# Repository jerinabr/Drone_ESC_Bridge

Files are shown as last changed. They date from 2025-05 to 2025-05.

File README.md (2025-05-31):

# Drone_ESC_Bridge
## Description
This board is intended to act as a bridge between the Nvidia Jetson and the 4-in-1 ESC on the ADP drone[^1]

It recieves motor speeds and other commands from the Jetson over the SPI interface and outputs motor speeds to the ESC over PWM

It also monitors the LiPo voltage and can report it back to the Jetson over the SPI interface

The board receives 5V power from an off-board buck converter which is used to power both the microcontroller (Seeed XIAO SAMD21) and the Jetson

[^1]: Firmware for the Jetson and Seeed XIAO can be found [here](https://github.com/LarsGart/Autonomous-Drone-Platform)

## BOM
| Reference | Value | Footprint | Qty | DigiKey Part Number |
| --- | --- | --- | --- | --- |
| C1,C2,C4,C6,C7,C8 | 0.1u | Capacitor_SMD:C_0603_1608Metric_Pad1.08x0.95mm_HandSolder | 6 | 311-1088-1-ND |
| C3 | 1u | Capacitor_SMD:C_0603_1608Metric_Pad1.08x0.95mm_HandSolder | 1 | 311-1446-1-ND |
| C5 | 22u | Capacitor_SMD:CP_Elec_6.3x5.8 | 1 | PCE3811CT-ND |
| ESC1 | Conn_01x08 | Connector_JST:JST_SH_BM08B-SRSS-TB_1x08-1MP_P1.00mm_Vertical | 1 | 455-BM08B-SRSS-TBCT-ND |
| ESC_DEBUG1 | Conn_01x06 | Connector_PinHeader_2.54mm:PinHeader_2x03_P2.54mm_Vertical | 1 | 2057-PH2-06-UA-ND |
| JETSON_PWR1 | Conn_02x02_Top_Bottom | Connector_PinHeader_2.54mm:PinHeader_2x02_P2.54mm_Vertical | 1 | 2057-PH2-04-UA-ND |
| Q1 | Si2318CDS | Package_TO_SOT_SMD:SOT-23-3 | 1 | SI2318CDS-T1-GE3CT-ND |
| R1 | 10m | Resistor_SMD:R_2010_5025Metric_Pad1.40x2.65mm_HandSolder | 1 | 13-PE2010FKE070R01LCT-ND |
| R2 | 100 | Resistor_SMD:R_0603_1608Metric_Pad0.98x0.95mm_HandSolder | 1 | 311-100HRCT-ND |
| R3 | 33k | Resistor_SMD:R_0603_1608Metric_Pad0.98x0.95mm_HandSolder | 1 | 311-33.0KHRTR-ND |
| R4 | 8.2k | Resistor_SMD:R_0603_1608Metric_Pad0.98x0.95mm_HandSolder | 1 | 311-8.2KGRTR-ND |
| SPI1,VBUCK1 | Conn_01x04 | Connector_PinHeader_2.54mm:PinHeader_2x02_P2.54mm_Vertical | 2 | 2057-PH2-04-UA-ND |
| U1 | LMP8640 | Package_TO_SOT_SMD:SOT-23-6 | 1 | 296-48927-1-ND |
| U2 | LM5050-1 | Package_TO_SOT_SMD:TSOT-23-6 | 1 | 296-46427-1-ND |
| XIAO_L1,XIAO_R1 | Conn_01x07 | Connector_PinSocket_2.54mm:PinSocket_1x07_P2.54mm_Vertical | 2 | S7040-ND |

> [!NOTE]
> `JETSON_PWR1` has the same part number has `SPI1` and `VBUCK1`\
> They're separate entries because the connector footprint used in the schematic was different

## Images
### Schematic
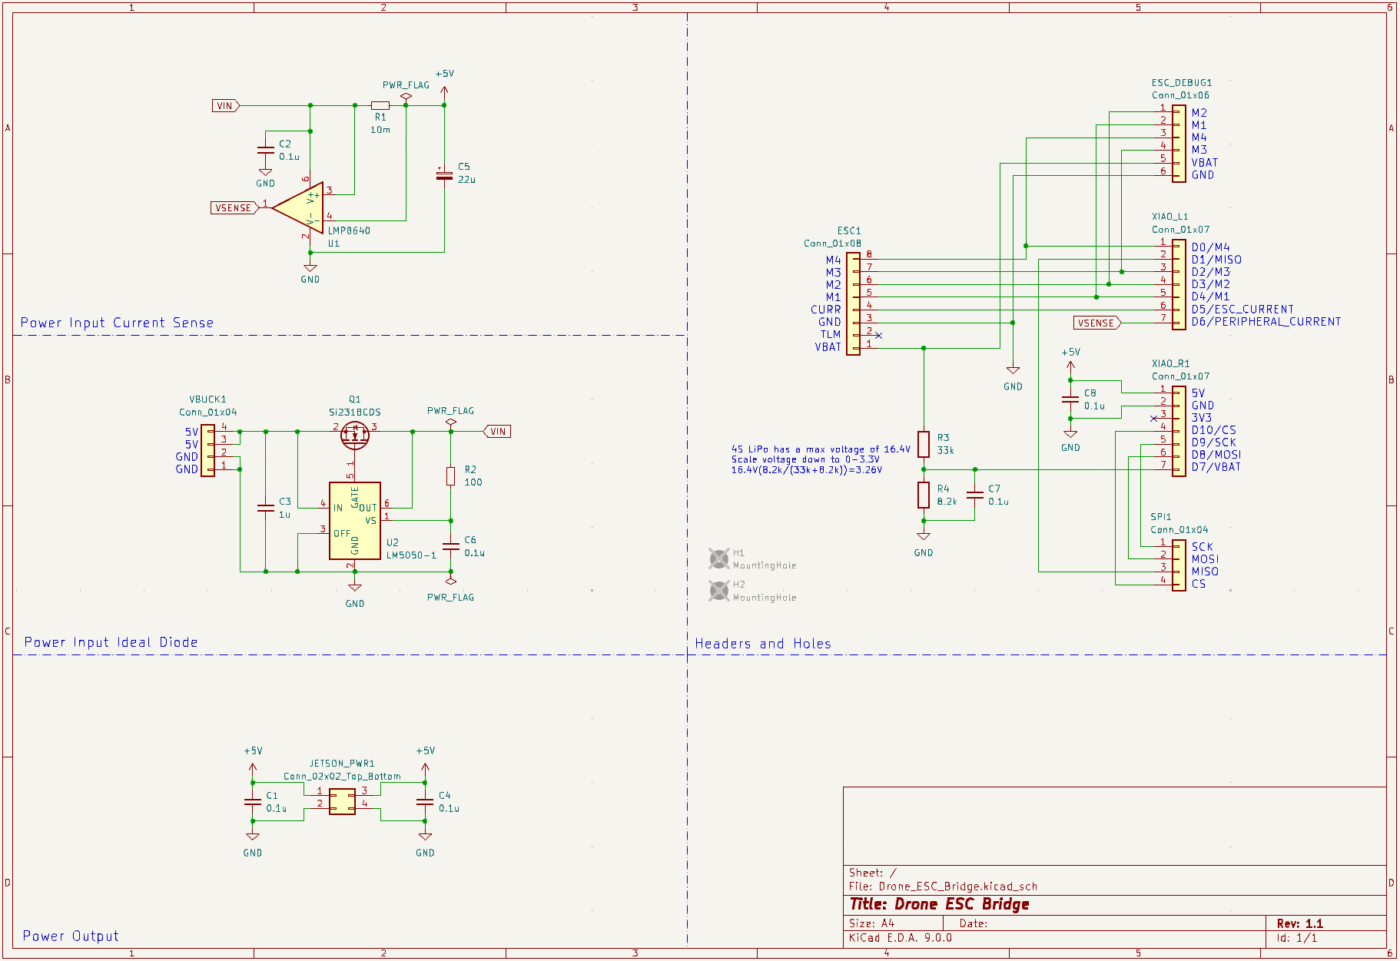
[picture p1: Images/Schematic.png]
Schematic Diagram

### Top Layer
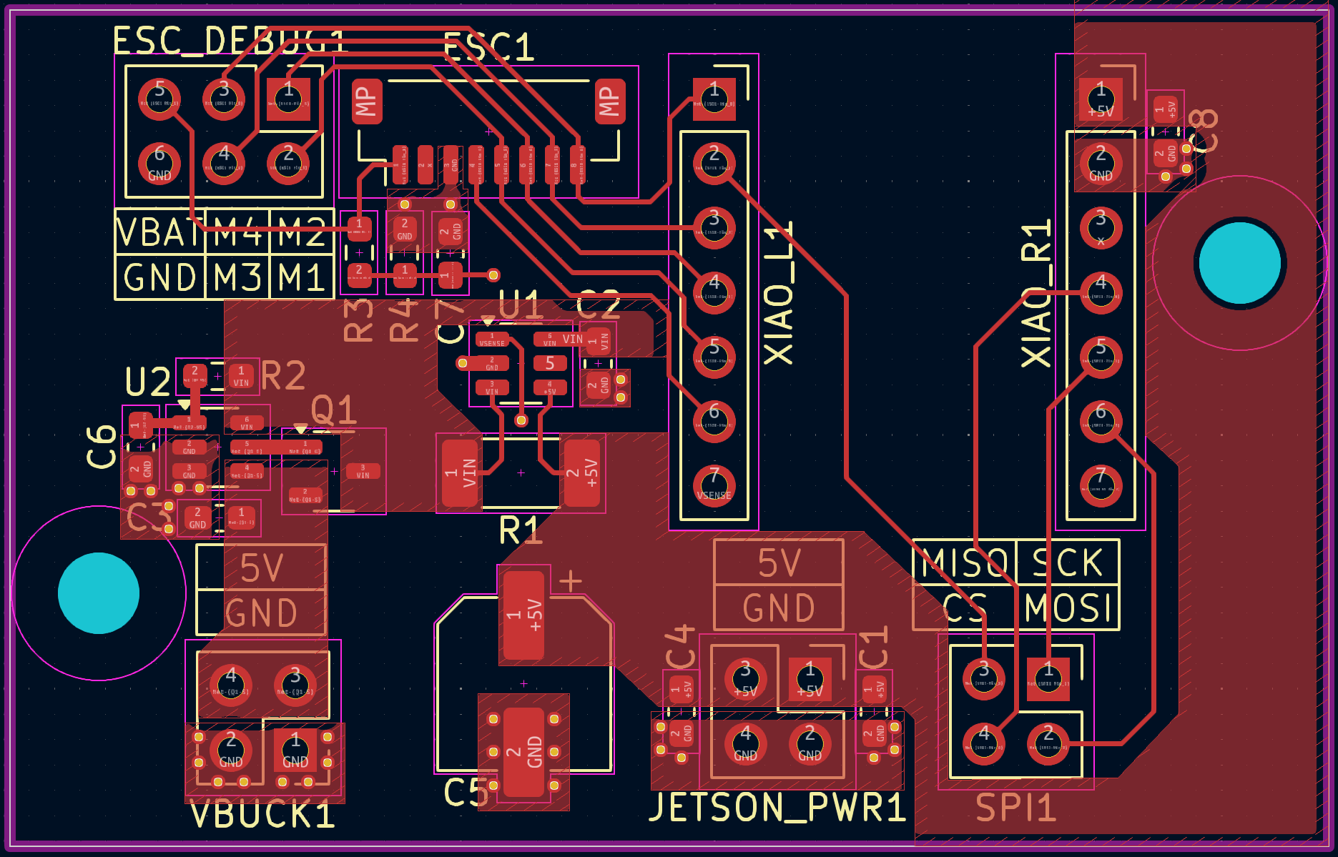
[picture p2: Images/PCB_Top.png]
PCB top layer with silkscreen

### Bottom Layer
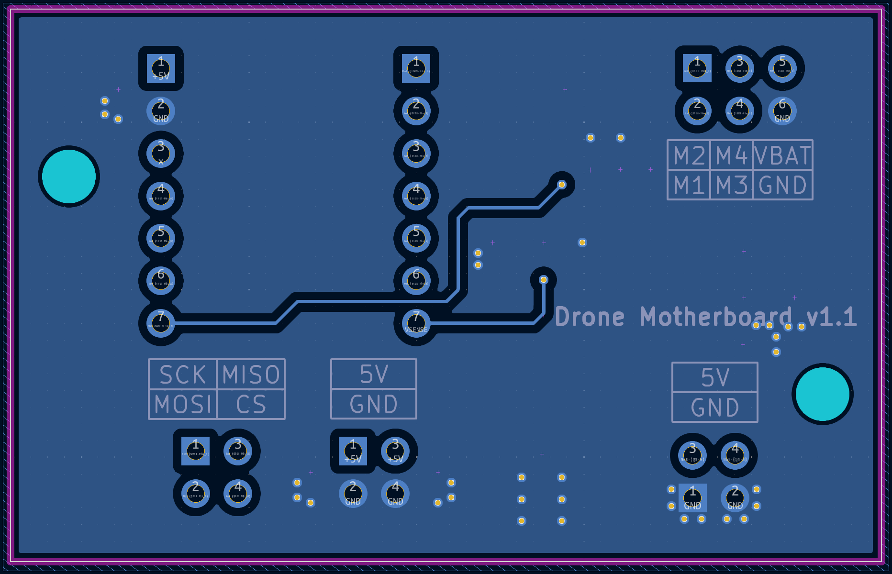
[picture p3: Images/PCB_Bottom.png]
PCB bottom layer with silkscreen

### 3D Top View
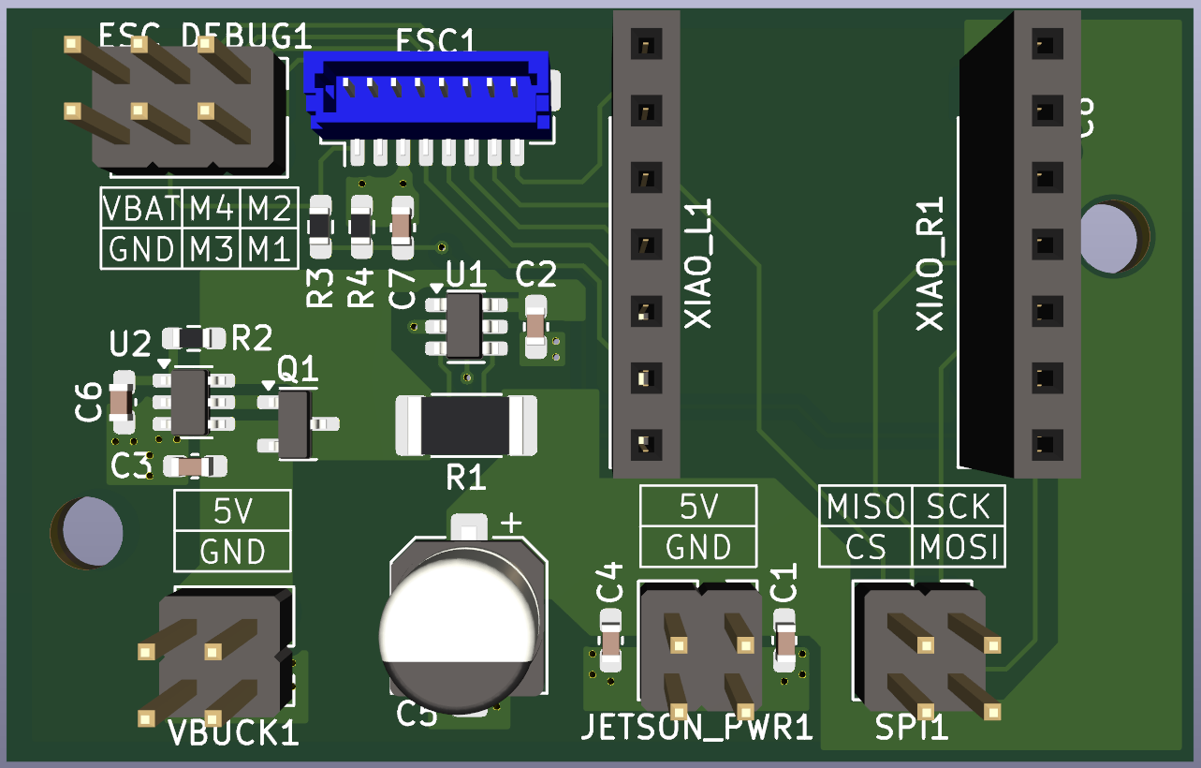
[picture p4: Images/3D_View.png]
3D view of the top of the board with components


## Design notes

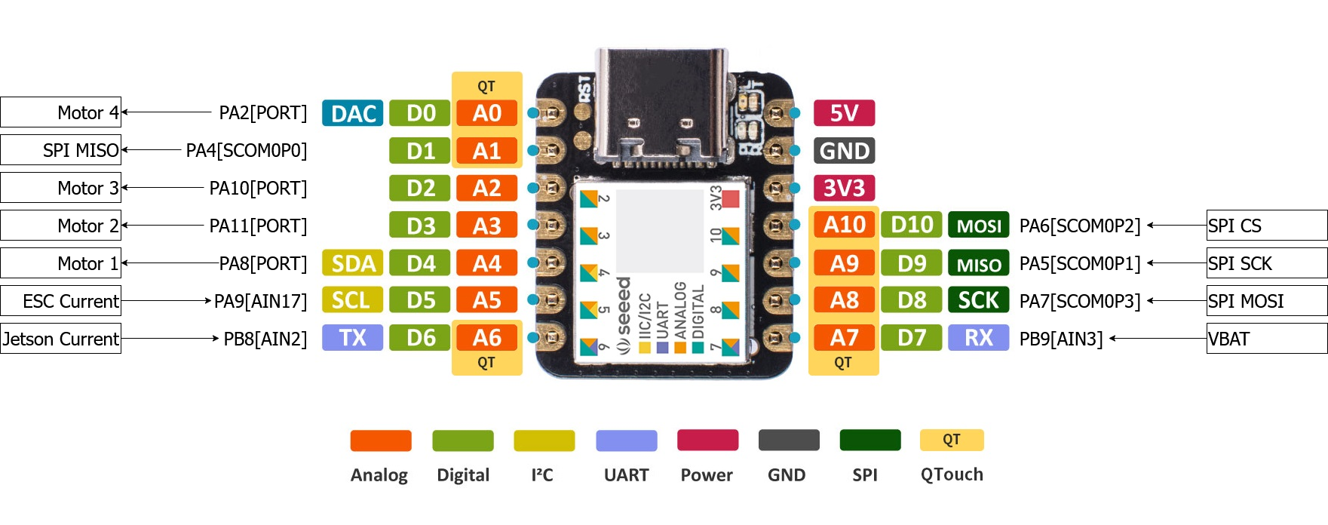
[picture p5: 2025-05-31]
MCU_Connection_Diagram.png

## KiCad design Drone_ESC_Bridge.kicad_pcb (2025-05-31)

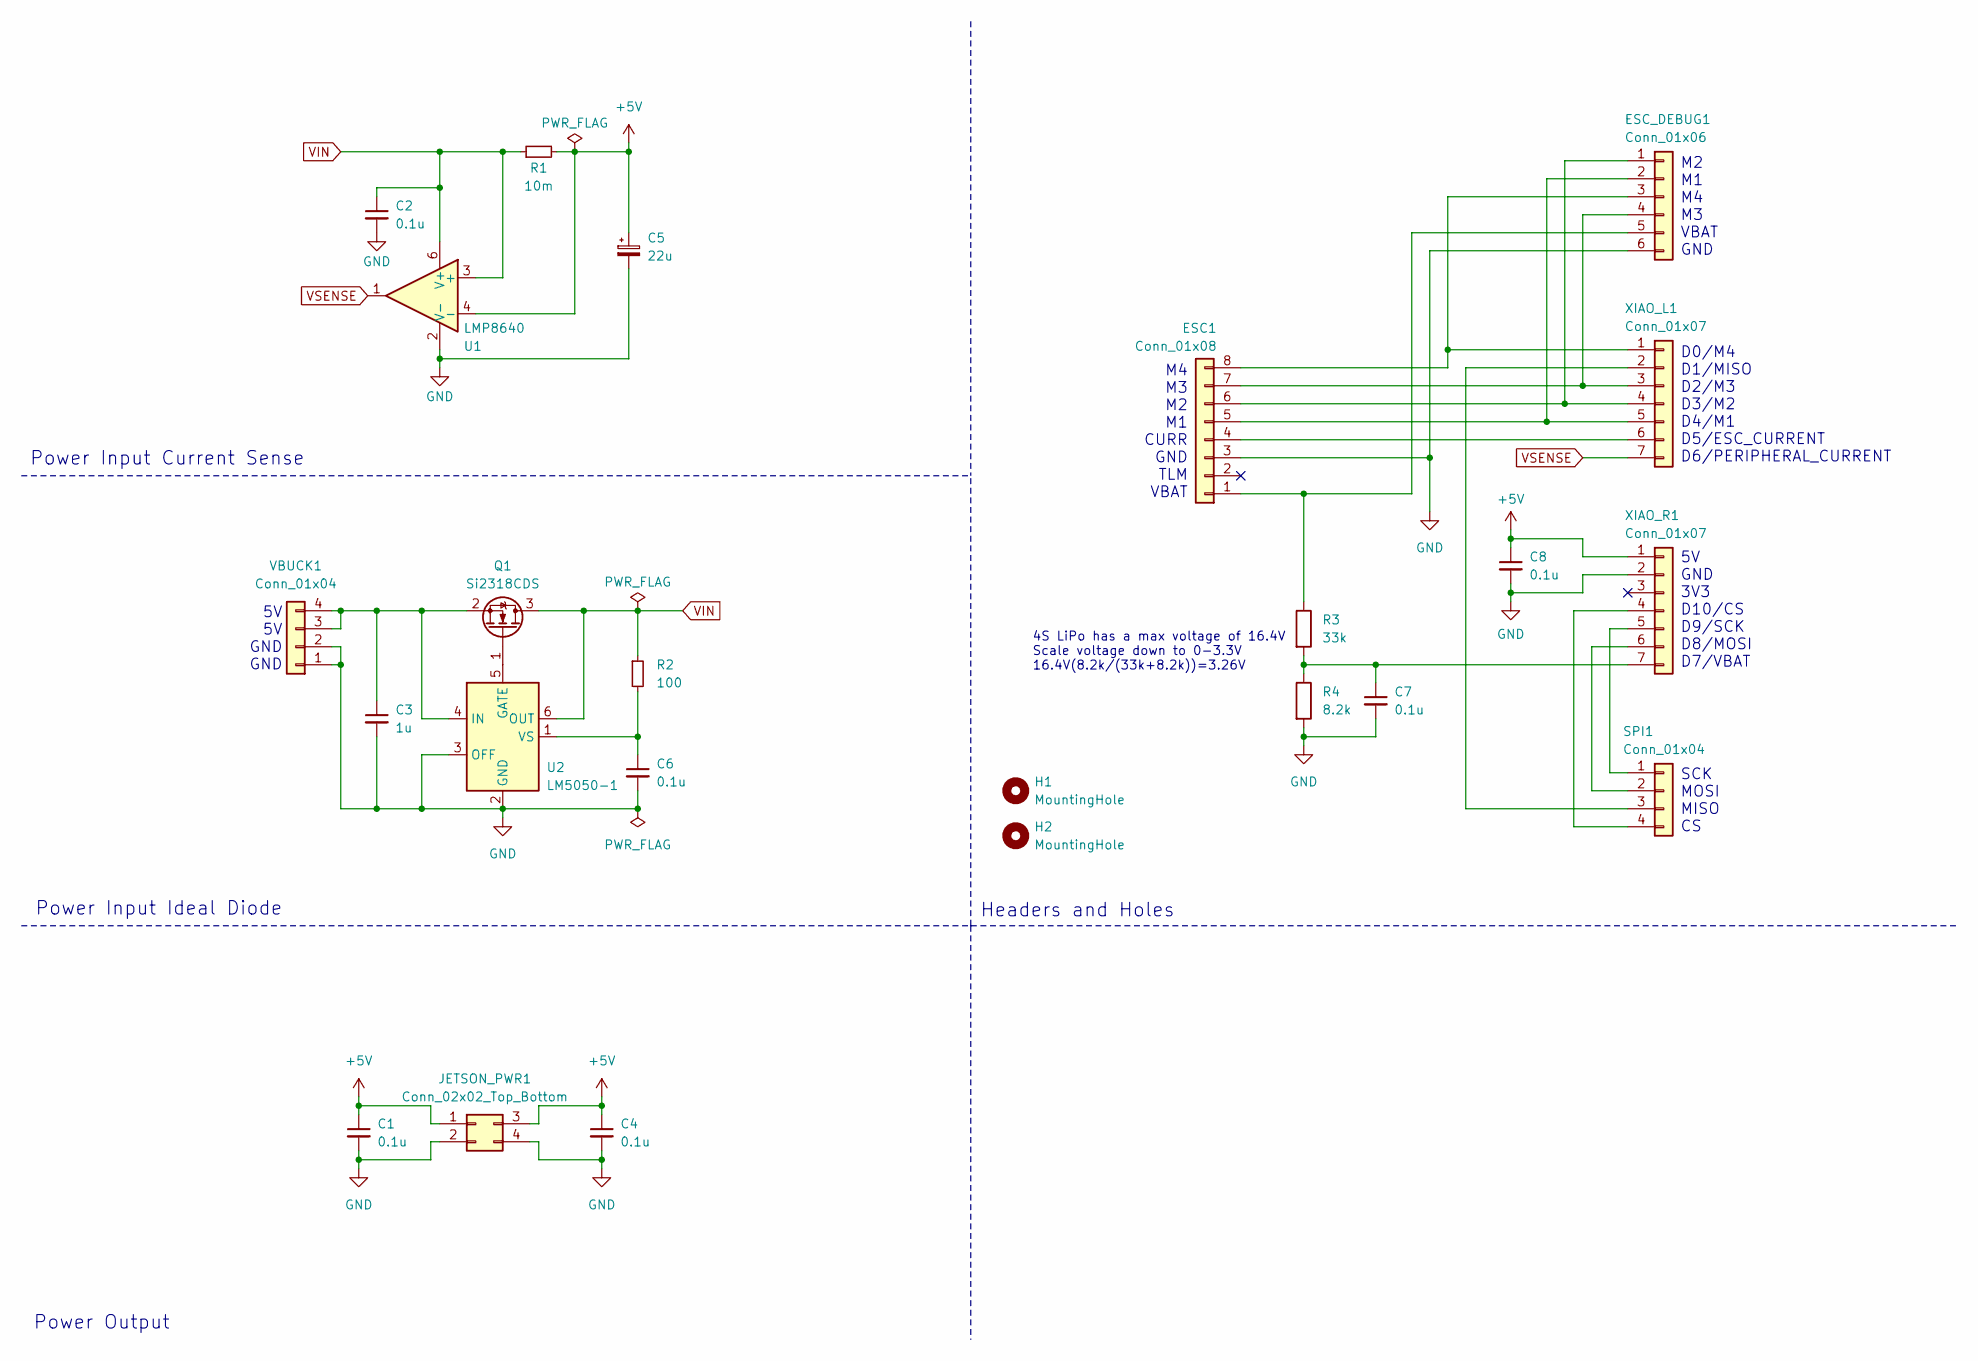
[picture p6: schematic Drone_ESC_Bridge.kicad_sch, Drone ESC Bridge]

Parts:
C1, C2, C4, C6, C7, C8: 0.1u; C_0603_1608Metric_Pad1.08x0.95mm_HandSolder; Part Number 311-1088-1-ND
C3: 1u; C_0603_1608Metric_Pad1.08x0.95mm_HandSolder; Part Number 311-1446-1-ND
C5: 22u; CP_Elec_6.3x5.8; Part Number PCE3811CT-ND
ESC1: Conn_01x08; JST_SH_BM08B-SRSS-TB_1x08-1MP_P1.00mm_Vertical; Part Number 455-BM08B-SRSS-TBCT-ND
ESC_DEBUG1: Conn_01x06; PinHeader_2x03_P2.54mm_Vertical; Part Number 2057-PH2-06-UA-ND
H1, H2: MountingHole; MountingHole_3.2mm_M3
JETSON_PWR1: Conn_02x02_Top_Bottom; PinHeader_2x02_P2.54mm_Vertical; Part Number 2057-PH2-04-UA-ND
Q1: Si2318CDS; SOT-23-3; Part Number SI2318CDS-T1-GE3CT-ND
R1: 10m; R_2010_5025Metric_Pad1.40x2.65mm_HandSolder; Part Number 13-PE2010FKE070R01LCT-ND
R2: 100; R_0603_1608Metric_Pad0.98x0.95mm_HandSolder; Part Number 311-100HRCT-ND
R3: 33k; R_0603_1608Metric_Pad0.98x0.95mm_HandSolder; Part Number 311-33.0KHRTR-ND
R4: 8.2k; R_0603_1608Metric_Pad0.98x0.95mm_HandSolder; Part Number 311-8.2KGRTR-ND
SPI1: Conn_01x04; PinHeader_2x02_P2.54mm_Vertical; Part Number 2057-PH2-04-UA-ND
U1: LMP8640; SOT-23-6; Part Number 296-48927-1-ND
U2: LM5050-1; TSOT-23-6; Part Number 296-46427-1-ND
VBUCK1: Conn_01x04; PinHeader_2x02_P2.54mm_Vertical; Part Number 2057-PH2-04-UA-ND
XIAO_L1: Conn_01x07; PinSocket_1x07_P2.54mm_Vertical; Part Number S7040-ND
XIAO_R1: Conn_01x07; PinSocket_1x07_P2.54mm_Vertical; Part Number S7040-ND

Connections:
+5V: C1.1, C4.1, C5.1, C8.1, JETSON_PWR1.1, JETSON_PWR1.3, R1.2, U1.4 (-), XIAO_R1.1
GND: C1.2, C2.2, C3.2, C4.2, C5.2, C6.2, C7.2, C8.2, ESC1.3, ESC_DEBUG1.6, JETSON_PWR1.2, JETSON_PWR1.4, R4.2, U1.2 (V-), U2.2 (GND), U2.3 (OFF), VBUCK1.1, VBUCK1.2, XIAO_R1.2
unnamed: ESC1.1, ESC_DEBUG1.5, R3.1
unnamed: ESC1.4, XIAO_L1.6
unnamed: ESC1.5, ESC_DEBUG1.2, XIAO_L1.5
unnamed: ESC1.6, ESC_DEBUG1.1, XIAO_L1.4
unnamed: ESC1.7, ESC_DEBUG1.4, XIAO_L1.3
unnamed: ESC1.8, ESC_DEBUG1.3, XIAO_L1.1
unnamed: Q1.1 (G), U2.5 (GATE)
unnamed: C3.1, Q1.2 (S), U2.4 (IN), VBUCK1.3, VBUCK1.4
unnamed: SPI1.1, XIAO_R1.5
unnamed: SPI1.2, XIAO_R1.6
unnamed: SPI1.3, XIAO_L1.2
unnamed: SPI1.4, XIAO_R1.4
unnamed: C6.1, R2.2, U2.1 (VS)
unnamed: C7.1, R3.2, R4.1, XIAO_R1.7
VIN: C2.1, Q1.3 (D), R1.1, R2.1, U1.3 (+), U1.6 (V+), U2.6 (OUT)
VSENSE: U1.1, XIAO_L1.7

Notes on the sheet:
M2 M1 M4 M3 VBAT GND
Power Output
4S LiPo has a max voltage of 16.4V Scale voltage down to 0-3.3V 16.4V(8.2k/(33k+8.2k))=3.26V
5V 5V GND GND
5V GND 3V3 D10/CS D9/SCK D8/MOSI D7/VBAT
Power Input Current Sense
M4 M3 M2 M1 CURR GND TLM VBAT
Power Input Ideal Diode
D0/M4 D1/MISO D2/M3 D3/M2 D4/M1 D5/ESC_CURRENT D6/PERIPHERAL_CURRENT
Headers and Holes
SCK MOSI MISO CS

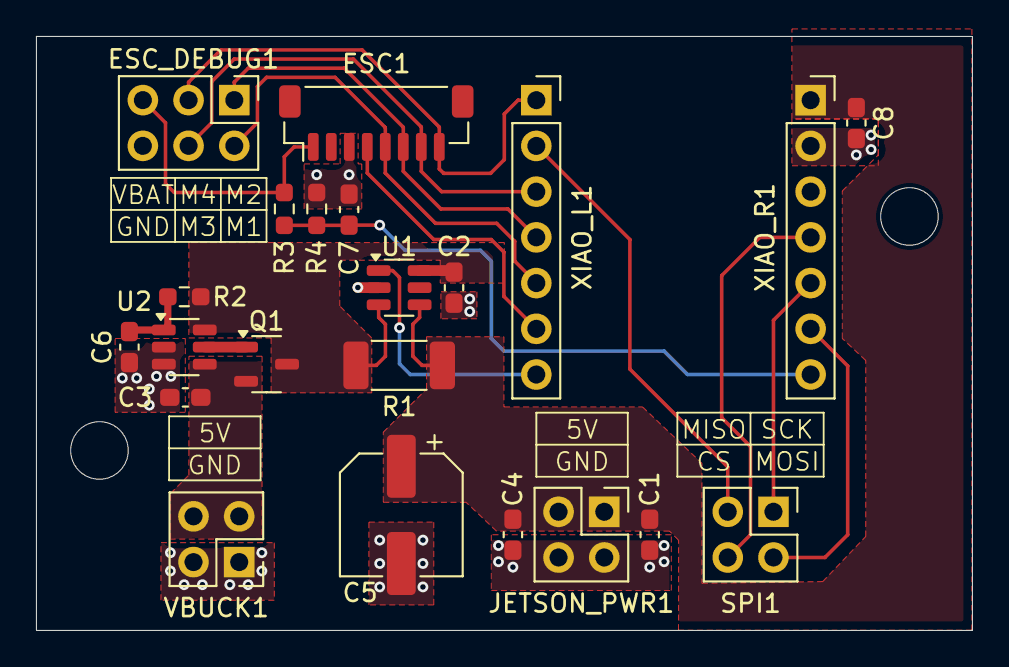
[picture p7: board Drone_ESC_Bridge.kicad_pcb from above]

Board: 2 copper layers, 52.0 x 33.0 mm, 24 parts (0 on the bottom side), 18 nets.

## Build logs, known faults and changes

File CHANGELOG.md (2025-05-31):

# Changelog
This is the revision history for the drone ESC bridge
## v1.1
### Schematic
- Changed the `ESC Telemetry` pin function to `Battery Voltage` because this board won't handle DShot telemetry requests
  - Change affected ESC_Debug header as well
- Added voltage divider circuitry to scale the 4S LiPo voltage (max 16.4V) to max 3.3V
- Remapped the XIAO connector pins because I didn't bother checking to see if the XIAO pins could support the function I assigned them to
  | Pin Function                | Previous Pin  | New Pin   |
  | --------------------------- | ------------- | --------- |
  | `Motor 1`                   | D3            | D4        |
  | `Motor 2`                   | D2            | D3        |
  | `Motor 3`                   | D1            | D2        |
  | `Motor 4`                   | D0            | Unchanged |
  | `ESC Current Sense`         | D4            | D5        |
  | `Peripheral Current Sense`  | D5            | D6        |
  | `Battery Voltage`           | D7            | Unchanged |
  | `SPI MOSI`                  | D10           | D8        |
  | `SPI MISO`                  | D9            | D1        |
  | `SPI SCK`                   | D8            | D9        |
  | `SPI CS`                    | D6            | D10       |
- Reordered the SPI connector pin functions to make the board routing a little easier
### Board
- Moved SPI connector closer to Jetson power connector
- Updated SPI connector silkscreen labels to reflect pin reordering
- Removed ground pour on top layer
  - Used polygon pours with stitching vias on ground pads instead
- Updated silkscreen pin info table for ESC_Debug to replace `TLM` with `VBAT`
### Misc
- Added this changelog file
- Added image of MCU connection diagram to the folder
## v1.0
Initial release

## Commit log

2025-04-04 Initial release
    [Drone_ESC_Bridge.kicad_pcb, Drone_ESC_Bridge.kicad_sch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]
2025-04-06 Initial board revision
    [Drone_ESC_Bridge.kicad_pcb, Drone_ESC_Bridge.kicad_sch]
2025-04-10 Make v in version silkscreen lowercase
    [Drone_ESC_Bridge.kicad_pcb]
2025-05-03 Replace telemetry with VBat sense
    [Drone_ESC_Bridge.kicad_pcb, Drone_ESC_Bridge.kicad_sch]
2025-05-03 Update gerbers
    [Drone_ESC_Bridge-B_Cu.gbr, Drone_ESC_Bridge-B_Mask.gbr, Drone_ESC_Bridge-B_Silkscreen.gbr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]
2025-05-04 Shrink ground polygon box
    [Drone_ESC_Bridge.kicad_pcb]
2025-05-31 Add BOM and update ibom
    [Drone_ESC_Bridge.kicad_pcb, Drone_ESC_Bridge.kicad_sch, Drone_ESC_Bridge_BOM.csv]
2025-05-31 Move BOM into bom folder
    [bom.csv]
